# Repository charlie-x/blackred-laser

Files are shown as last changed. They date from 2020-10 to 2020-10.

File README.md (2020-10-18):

# blackred-laser
anything i do for the black/red/redsail/orion motor tech lasers 

for the zZ table mod

* nema 17 motor 1.7A  http://www.zyltech.com/nema-17-stepper-motor-1-7-a-0-59-nm-84-ozin-1-3-or-5-pack/
* step/dir driver for motor https://www.amazon.com/UsongShine-Stepper-Controller-Arduino-Printer/dp/B07HHS14VQ/ only needs to be set to 0.7A
* pulleys and belts https://www.amazon.com/gp/product/B07ZBZ739T/ motor is 5 mm shaft is 7mm  i used 20T/60T and drilled out the larger pulley to a 7mm bore size. 6mm belt. unfortunately i had all the parts lying around to do this so i can't give the exact buy links. 
* two m5 bolts 10mm length , washers and nuts
* 4 m3's 6mm for the motor
* 1/8th plywood cut out
* two holes drilled in metal frame to mount the motor plate, clearance holes for 5mm bolts, 11mm from front end (furthest from bed) 18mm apart.
* sheet of 5mm rubber foam to go between the motor and the steel frame to dampen any vibration
* write to ruidia , step-/dir - and 5v to both dir+/step+ 
* 3 pin 100 phoenix connector https://www.amazon.com/gp/product/B07TQLYQ7W/
* ferrules on wires for the phoenix, https://www.amazon.com/gp/product/B07XBLGPCY llike this
* add power, piggybacked off one of the existing drivers
* routed through existing holes.
* configure z

link to fusion model for the plate https://a360.co/31iYAaa (slightly newer than dxf, but only diff is rounded corners)
and a dxf https://github.com/charlie-x/blackred-laser

* sketch of hole positions etc https://i.imgur.com/GI5tMqN.png
* foam sheet https://i.imgur.com/nw5YQlq.png
* back view https://i.imgur.com/fHuTyGB.jpg
* https://i.imgur.com/ZtqozoY.png nuts underneath
* drive power tapped from here https://i.imgur.com/az9yAoT.jpg (inital testing)
* dir/step/5v to the driver, go here https://i.imgur.com/dZJjmzx.jpg (inital testing)
* stepper driver wiring https://i.imgur.com/Y4kkJVZ.jpg connect motor phases per your stepper

* ena-/ena+ aren't used since enable on is default
* dir- to controller dir- 
* dir+ to controller +5v
* pul- to controller pul- 
* pul+ to controller +5v
* gnd to gnd on existing driver or main PSU
* VCC to power on existing driver, or main PSU. 24V make sure the driver you buy takes 24V, most do

set the current to 1.7A peak, start off with step set to 1 and make sure it moves, then step down.

since every table will be slightly different specs you may not be able to run down to 16/32 microstepping. make sure to set the acceleration in the controller. i inverted the keypad direction in the controller

only mods to the laser are the two holes for the M5 bolts , so 5.4mm drill or so.

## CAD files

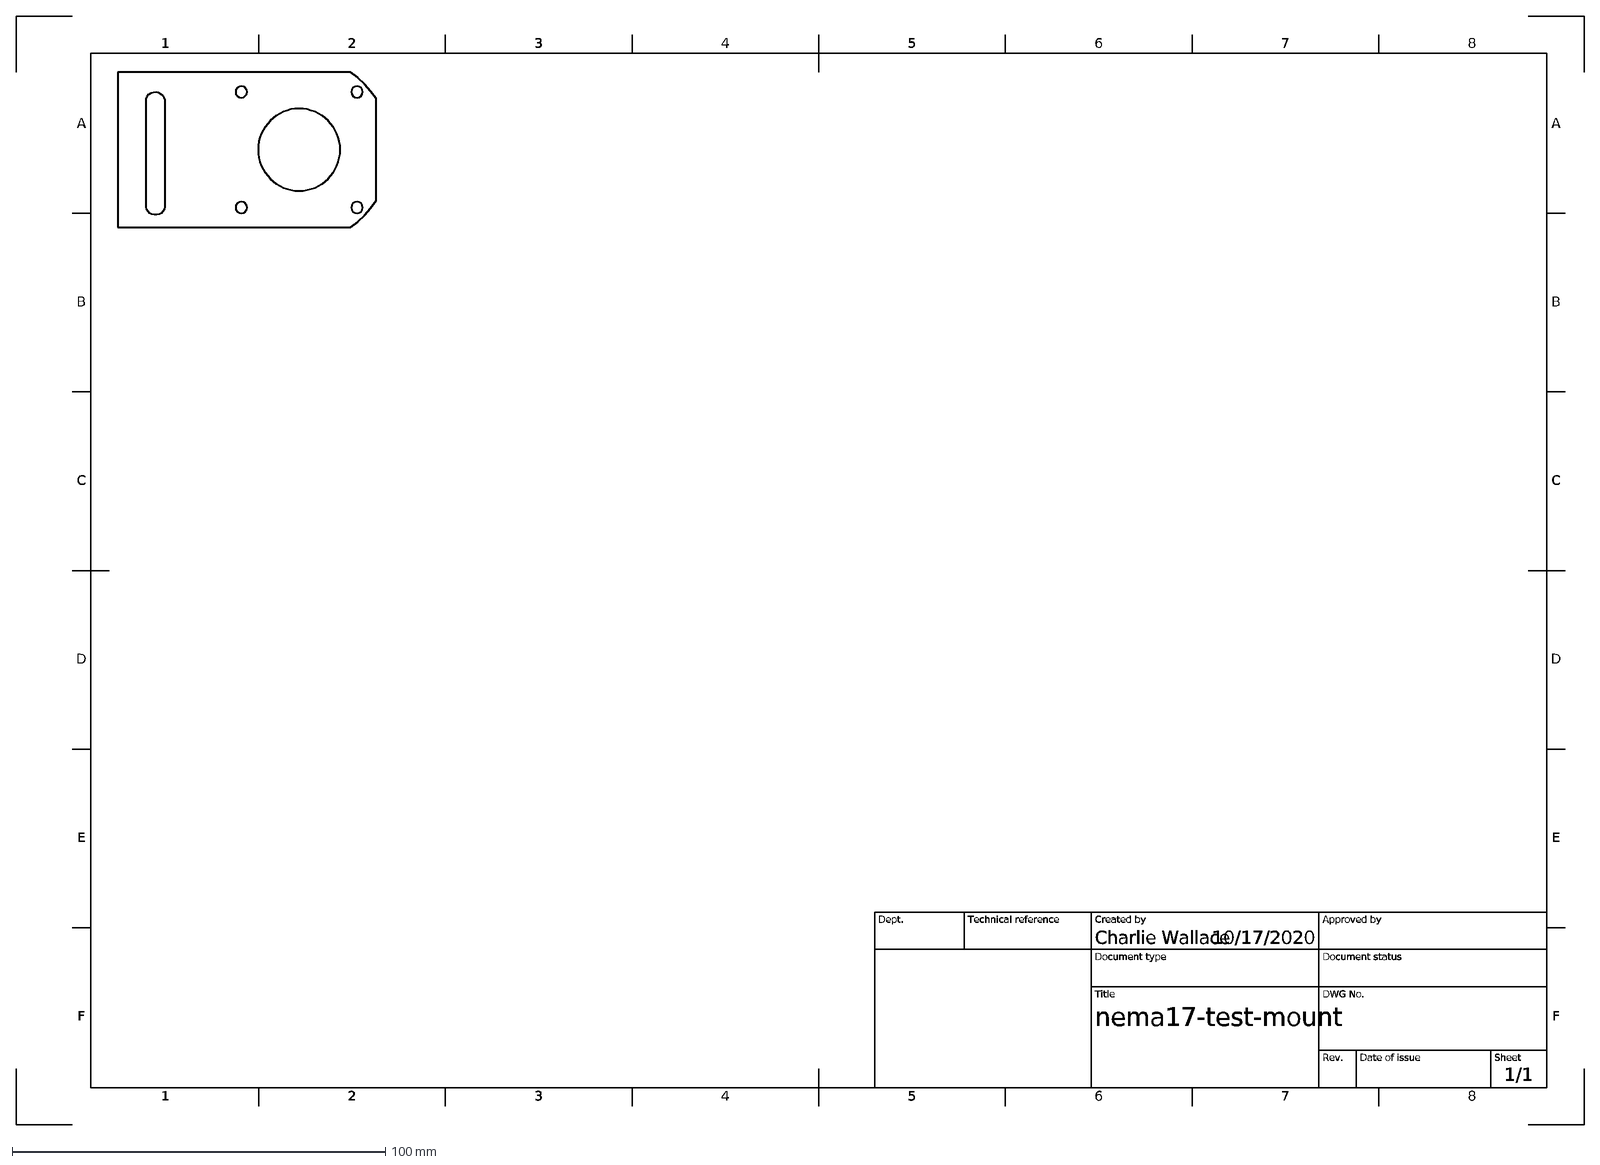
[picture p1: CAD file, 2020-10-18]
nema-17mount.dxf
1
A
2
3
4
5
6
7
8
B
C
D
E
F
10/17/2020
1/1
nema17-test-mount
Charlie Wallace
Dept.
Technical reference
Created by
Approved by
Document type
Document status
Title
DWG No.
Rev.
Date of issue
Sheet

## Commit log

2020-10-18 laser cut for nema 17
    [nema-17mount.dxf]
2020-10-19 holddowns
    holddowns that stick in the honeycomb,
    originals https://community.glowforge.com/t/honeycomb-bed-holdown-pins/18652
2020-10-25 z focus test
    grid of boxes that step down at .1mm increments to test focus
